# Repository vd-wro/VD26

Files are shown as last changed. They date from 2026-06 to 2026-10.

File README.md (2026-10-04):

# WRO VizDrive 2026


 

Welcome to the project repository for the **Panamanian 🔴⚪🔵 Team VizDrive** for the **World Robot Olympiad (WRO)** 2026!
Here you will find all the documentation, source code, images, and models related to our autonomous robot.

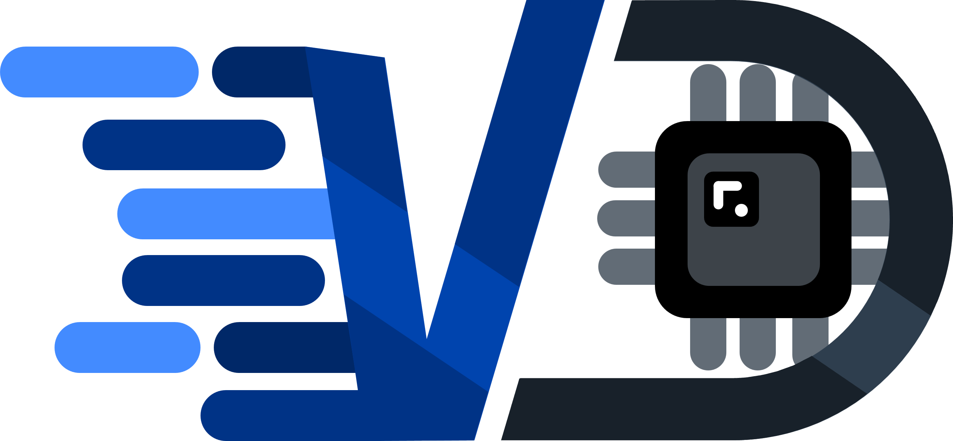
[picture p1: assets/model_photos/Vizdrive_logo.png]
Vizdrive Logo)


## About VizDrive's Legacy

VizDrive started in 2025, and now keeps thriving with the same young Panamanians that started the project. For this updated 2026 repository, we have kept ViZio's previous versions for better understanding and comparison from our engineering process.

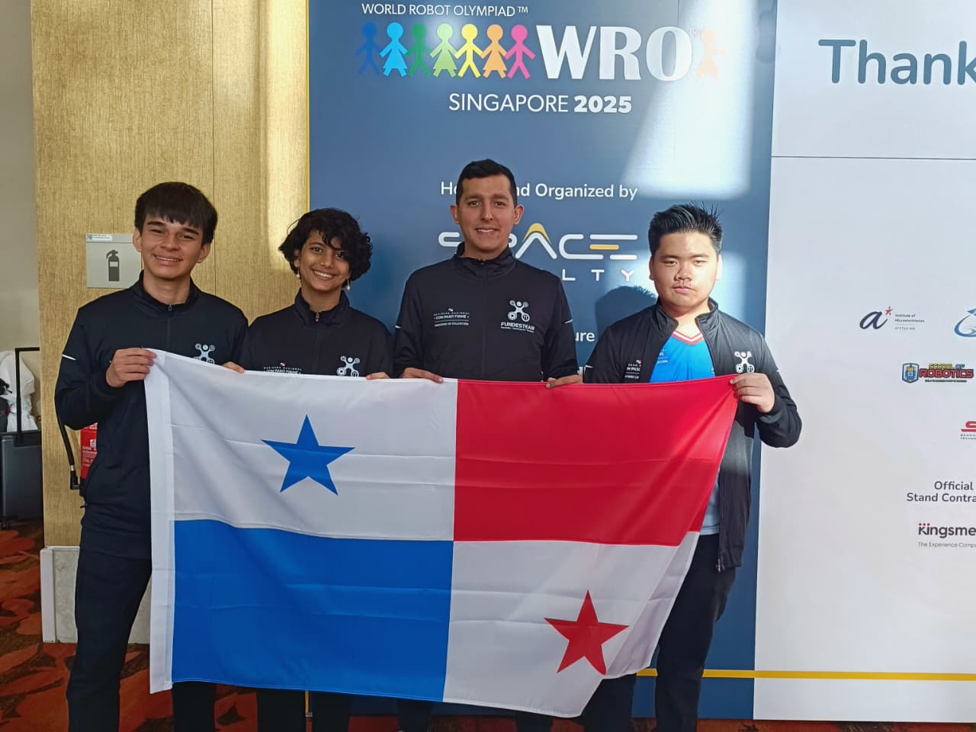
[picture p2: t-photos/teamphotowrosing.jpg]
Team


## Project Summary

VizDrive's core, ViZio, is an autonomous robot designed to navigate a closed-loop circuit, maintaining a stable trajectory with gyroscopic correction. It uses artificial vision, in conjunction with ultrasonic and color sensors, to detect walls and avoid obstacles.

Vizdrive Overview

We are participating in the **Future Engineers Category** to develop our skills and demonstrate the capabilities of young Panamanians in a competitive field like robotics.

During the creation of our robot, we tried to push the **fundamentals of robotics** to the highest we could. As you go through this GitHub repository, you may notice that we worked with very basic sensors (the kind typically found in standard Arduino kits), and that we strived to optimize them to the best of our capacities. This is because we aimed to make our build accessible for everyone, and show that even with the simplest components, it is possible to create truly functional robotic systems.

We would like to invite you into this short, 3 minute summary video to have a fresh start on our robot's construction, logic, and GitHub organization.

ViZio IV (https://www.youtube.com/watch?v=sTCSiO5S7kA)

> [!NOTE]
> Throughout the competition, we are constantly making modifications in the software and hardware of our robot. We try to update on all the changes we make, but if you notice any inconsistency between the pages of the documentation, please let us know!

---

## General Project Index

You can use this index to navigate through our robot's documentation. Each document provides detailed information on every aspect of its operation:

* [**1. General Project Overview**](./docs/01_project_overview.md)
  * General and concise introduction to the robot and its main components.
  * Describes the robot's operational phases and workflow diagram.
* [**2. Hardware and Components of the Robot**](./docs/02_hardware_components.md)
  * Detailed specifications of all integrated electronic and mechanical hardware.
  * [General Electromechanical Diagram](./schemes/electromechanical_diagram.png)
  * [Circuit Interactive Design (Cirkit)](https://vd-wro.github.io/VD26/embeds/interactive_circuit)
  * [KiCad Files](./src/kicad_pcb)
* [**3. Software Architecture**](./docs/03_software_architecture.md)
  * Overview of software libraries, core functionalities, and code structure.
  * [Autonomous Driving Code](./src/main_control/Vizdrive_WRO_code.ino)
* [**4. Sensor and Pin Configurations**](./docs/04_sensors_and_pin_configuration.md)
  * In-depth review of each sensor, its role in the functionality, and Arduino pin assignments.
  * [Sensors' Test Codes](./src/test_code/)
* [**5. Robot Mobility Functionality**](./docs/05_robot_mobility.md)
  * Focuses on the robot's motion system, motor configuration, and steering mechanisms.
* [**6. PID Control for the Gyroscope**](./docs/06_pid_gyroscope_control.md)
  * Explains the MPU gyroscope implementation and PID control for trajectory stability.
  * [MPU Calibration Code](./src/mpu_orientation_control/mpu_calibration/mpu_calibration.ino)
  * [MPU Calibration Data Graph](./assets/data_graphs/MPU%20Calibration%20Data%20Analysis.xlsx)
* [**7. Computer Vision Functions**](./docs/07_computer_vision.md)
  * Covers the PixyCam's vision-based obstacle evasion.
  * [Computer Vision Code](./src/computer_vision/computer_vision.ino)
* [**8. Ultrasonic Distance Sensing and PID**](./docs/08_ultrasonic_distance_sensing.md)
  * Covers the distance measurement and wall avoidance with ultrasonic sensors, and the filters implemented to adjust precision.
  * Introduces and explains the side PID system for straight-line driving.
  * [Ultrasonic Sensor Data Analysis](./assets/data_graphs/Ultrasonic%20Sensors%20Data%20Analysis.xlsx)
* [**9. Color Detection Functions**](./docs/09_color_detection.md)
  * Explains the color sensor's applications and calibration.
* [**10. 3D Modeling and Fabrication**](./docs/10_3d_modeling.md)
  * Details the 3D design process, mechanical characteristics, and fabrication parameters.
  * [3D Models STL](./models/)
* [**11. Other Resources and User Manual**](./docs/11_other_resources.md)
  * User manual for robot's construction and operation.
  * Summarized documentation and additional relevant resources and materials.
  * Evolution and improvements made within the versions of the robot.
  * Technical issues and applied fixes.

---

## ViZio Versions

| Versions | Problems | Improvements made | Used In | 
| :--- | :--- | :--- | :--- |
| Prototype | Often finding disconnected components. | N/a | First prototype made. |
| ViZio | Gyroscope calibration, partial parking, connection problems due to cable wear, complications with the dual ultrasonic sensor. radar. | Removed clutter with a hand-soldered PCB. | 🇵🇦 Regionals 2025 |
| ViZio 2.0 | Challenges with Pixy Parameters' calibration, incomplete parking maneuver, inverted SDA and SCL pins. | Improved PCB, kept one frontal ultrasonic, new logic for parallel parking. | 🇵🇦 National 2025 |
| ViZio V3 | Block color detection through Pixy, slower velocity. | Fixed PCB, adaption to camera bug, new parallel parking logic that includes last block evasion. | 🇸🇬 WRO 2025 |
| ViZio IV | Poor power distribution caused servo peaks to drain the battery | Changed camera, improved chassis, upgraded PCB, and added mechanical differential. | 🇵🇦 Regionals & National 2026 |
| ViZio Phase V |  N/a  | Coming soon... | 🇵🇷 WRO 2026 |

For better comprehension please visit [**Previous Versions of our Robot**](./docs/11_other_resources.md#119-version-history)

---

## Photos and Videos

* **Team Photos:** [View Photos](./t-photos/README.md)
* **Vehicle Photos:** [View Photos](./v-photos/README.md)
* **Demonstration Videos:** [View Videos](./video/README.md)

---

## Source Code

All control and test codes are located in the `src/` folder.

* [Autonomous Driving (Obstacle Avoidance)](./src/main_control/Vizdrive_WRO_code.ino)
* [Autonomous Driving (No Obstacle Avoidance)](./src/main_control/Open_Round.ino)
* [MPU Orientation Control (PID and Calibration)](./src/mpu_orientation_control/pid_gyroscope.ino)
* [Computer Vision (PixyCam 2.1)](./src/computer_vision/computer_vision.ino)
* [Sensors' Test Codes](./src/test_code/)

---

## 3D Models

Files for 3D printed components are located in the `models/` folder in `.stl` files.
To access interactive models of each component, hosted in GitHub pages, visit `embeds/`.

* [Robot 3D Models](./models/)
* [Interactive 3D Models](./embeds/)

A version of our Unity Simulator, used during the robot's construction and planification process, is available as an HTTP embed, hosted with GitHub pages.

* [Unity Simulator Information](./embeds/Unity_simulator)
* [Unity Web Player](https://vd-wro.github.io/VD26/embeds/Unity_simulator/)

---

## Diagrams and Graphs

Flowcharts, circuits, and relevant data graphs.

* [Operation Flowcharts](./assets/flowcharts)
* [Calibration Data Graphs](./assets/data_graphs/)
* [Additional Hardware Photos](./assets/hardware_photos/)

---

## Team Members 🙋‍♂️🙋‍♀️🙋

| | | |
|:---:|:---:|:---:|
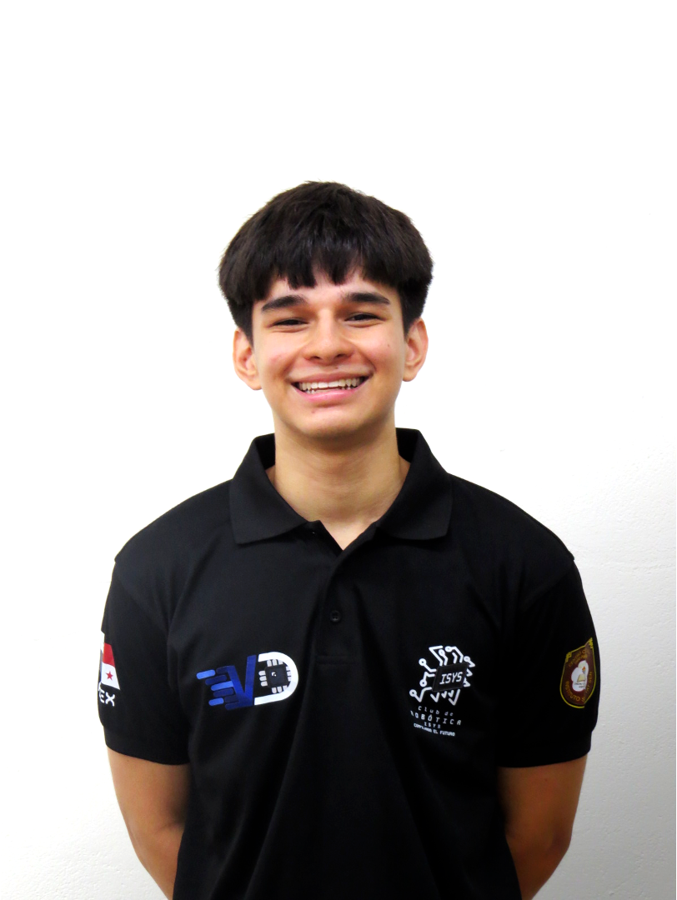
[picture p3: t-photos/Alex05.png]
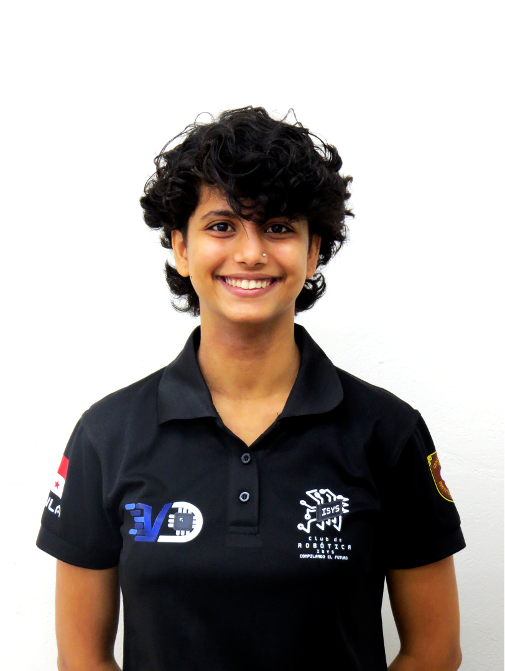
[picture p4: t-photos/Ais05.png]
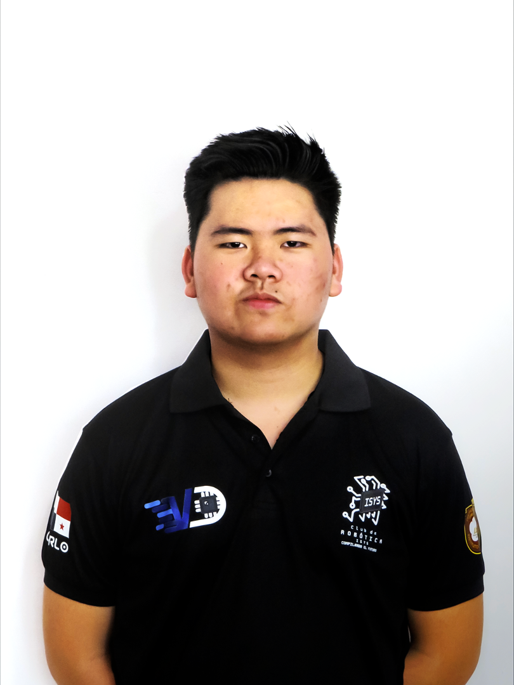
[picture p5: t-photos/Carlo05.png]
|  |  |  |
| [**ALEXIS PALACIOS NG**](./t-photos/meet_the_team/Alexis.md) <br> *Software Engineer* | [**AISLINN CHAWLA ARORA**](./t-photos/meet_the_team/Aislinn.md) <br> *Logistics and Creativity* |  [**CARLO HO NG**](./t-photos/meet_the_team/Carlo.md) <br> *Hardware Engineer* |
Sensor Integration, <br>Firmware Architecture, <br>Code Logic, <br>Error Management, <br>Data Analysis, <br>GitHub Repository | Engineering Journal, <br>Photography and Film, <br>Competition Planning, <br>Drafting, <br>Soldering, <br>GitHub Repository|  Construction, <br>Wiring, <br>Circuit and PCB Design, <br>Power Management, <br>3D Modeling and Planning, <br>Animation, Illustration, Editing  |

---

## Special Thanks

We are profoundly thankful to everyone who has supported us on our journey so far! We're incredibly grateful to our school administration for providing the resources and trust needed to pursue this challenge. To our teachers, thank you for your guidance and advice during our preparation; we especially appreciate your patience with our absences for robot practices (we promise to catch up on our assignments after the Olympiad 😅). A special shout-out to our friends who spent their free time supporting us, cheering us on, and helping us stay up to date. To our amazing parents, your assurance and belief in us have been the foundation of our efforts, allowing us to participate even though it meant missing many classes. And last but certainly not least, to our incredible coach, Professor Agustín Rogelio Orro Pérez. Even while mentoring five other teams, you still found time to guide us through it all. Your expertise, leadership, and dedication have been invaluable for us.

Thank you all!

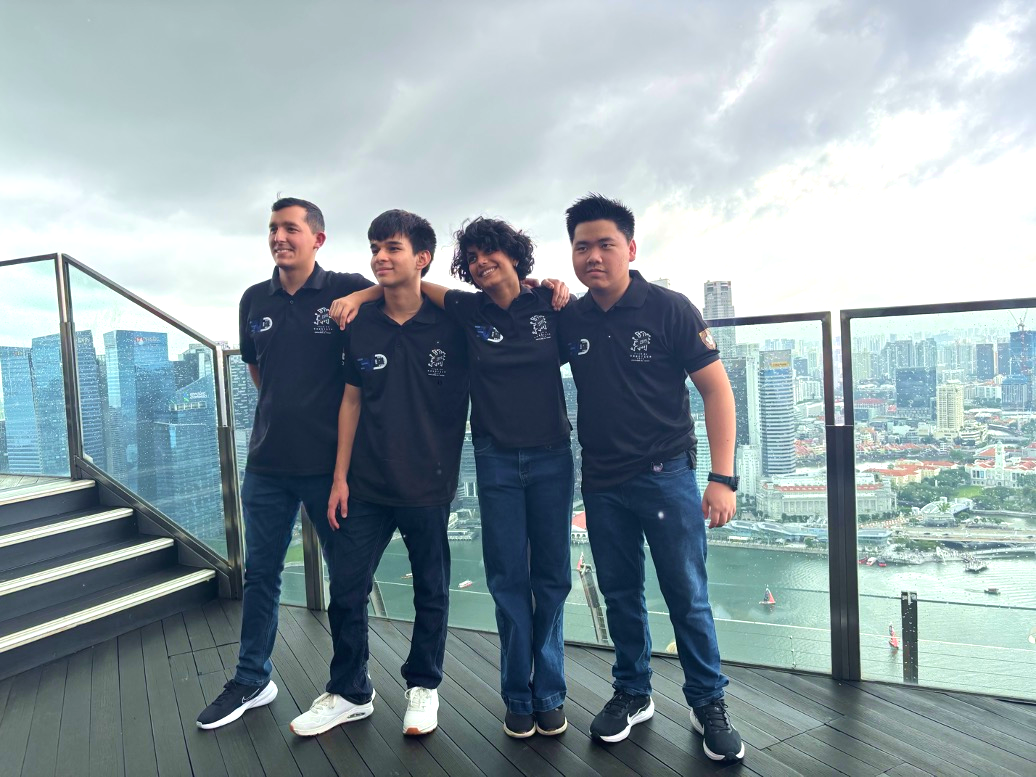
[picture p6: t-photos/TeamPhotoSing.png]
The Team


---

For any inquiry, question, or recommendation, feel free to contact us via email: **<vizdrive.wro@gmail.com>**

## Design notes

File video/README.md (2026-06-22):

# Robot Driving Demonstration Videos

Here are videos demonstrating our robot's autonomous driving capabilities for the WRO competition.

---

## Open Challenge Round Video

This video illustrates our robot's **MPU-6050 with PID orientation control**, coupled with **ultrasonic trajectory correction**.

For the Open Round, we adjusted our strategy because touching the outermost wall is prohibited. The robot's behavior in this video differs slightly from the complete code's. This adaptation is specifically for the Panamanian regional rounds, where the **center circuit configuration remains consistent**. In the full code, the robot prioritizes staying closer to the outermost wall to adapt to various environments.

Open Challenge Video (https://www.youtube.com/watch?v=nUoTaL3pmQw)

Previous versions of the robot share the same Open Round code and behavior; however, ViZio V3 now is able to navigate trough tighter spaces with the variable center.

Obstacle Challenge Video1 (https://www.youtube.com/watch?v=Y4y8UubQgvo)

---

## Obstacle Challenge Round Video

This video primarily showcases our robot's **artificial vision capabilities** using the **PixyCam 2.1**. It also features trajectory correction based on the MPU and PID control, supplemented by intentionally colliding with the outermost wall for a hard correction. If you observe closely, you'll also notice the subtle ultrasonic correction, which ensures the PixyCam consistently detects obstacles and reacts appropriately.

Updated regional practice video:

Obstacle Challenge Video1 (https://www.youtube.com/watch?v=GUYxAUy47Ms)

National close-up practice video:

Obstacle Challenge Video2 (https://www.youtube.com/watch?v=BSdScv6dc1I)

International event practice video:

Obstacle Challenge Video3 (https://www.youtube.com/watch?v=nUtFuM8RD_c)

You can also check our YouTube channel for more Obstacle Challenge videos.

# Robot Animation Video

These videos serve as supplementary material and explanations of the robot's assembly.

This video shows how to assemble all ViZio's parts and components into the chassis 3D Model.

Robot Animation Video1 (https://www.youtube.com/watch?v=Cte4G7Wkx94)

The second video explains all the changes made to our robot's updated version.

Robot Animation Video2 (https://www.youtube.com/watch?v=JOWvUNmzN1w) 

This is the third video, explaining the building process of ViZio's 3rd version.

Robot Animation Video3 (https://www.youtube.com/watch?v=J1BOTFqHlQ4) 

Fourth video, an introduction of what our latest model's improvements

ViZio IV (https://www.youtube.com/watch?v=X2UGbEu-D34)

Differential assembly video, an animation of the building process of ViZio's new mechanical differential system.

ViZio IV (https://www.youtube.com/watch?v=UHFCzMF-fk8)

# Music Creation Video (Easter egg!)

Not only the 3D models are created by us, the music as well is a personal composition for each video!
Soon the video explaining the music creation process will be uploaded to our Instagram Profile. 



---

[Back to Main README.md Index](../README.md)

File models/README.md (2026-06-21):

# Models Folder

Here you can find all the .stl and .glb models of every 3D modeled part of our robot.

The .glb models are used for the HTML embeds hosted in GitHub pages. 
We designed these embeds for a more interactive visualization of the models and their colors in the real-life robot. However, the .stl files can also be visualized directly in GitHub.

The designs included in this file directory are:

## 1. Chassis Model

| Old Model | New Robot | International Robot | 2026 Robot |
| :---: |  :---: |  :---: |  :---: |
| [Chassis](./chassis/chassis.stl) | [New Chassis](./chassis/chassis2.0.stl) | [International Chassis](./chassis/ViZioInternationalMotorFix.stl) | [2026 Chassis Moddels](./../docs/10_3d_modeling.md#chassis) |
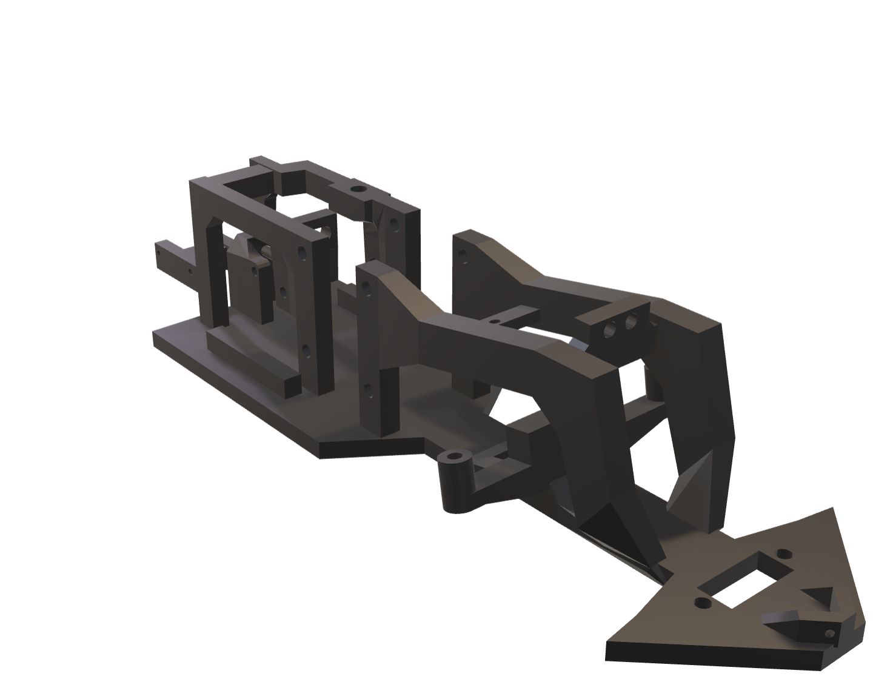
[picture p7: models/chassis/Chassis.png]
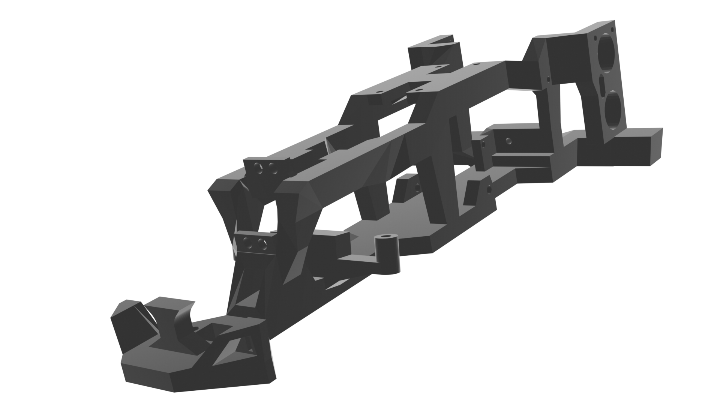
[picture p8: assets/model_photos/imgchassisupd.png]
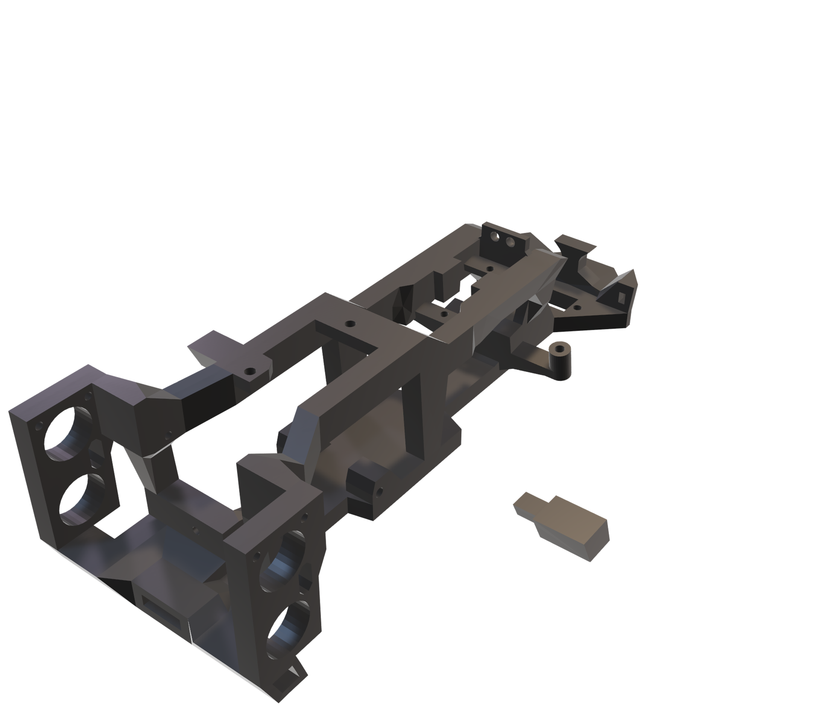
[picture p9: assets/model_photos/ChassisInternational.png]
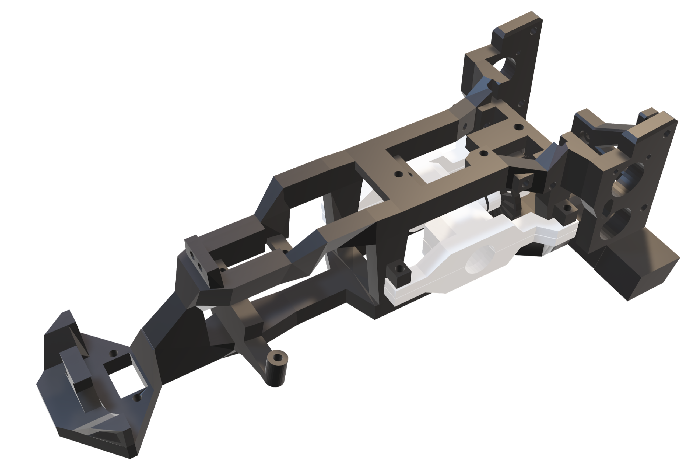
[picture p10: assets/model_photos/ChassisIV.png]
|  |  |  ||
| Visit the embed: [Chassis Embed](https://vd-wro.github.io/VD26/embeds/interactive_chassis)| Visit the updated embed: [Updated Chassis Embed](https://vd-wro.github.io/VD26/embeds/interactive_chassis2) | Visit the latest version: [International Chassis Embed](https://vd-wro.github.io/VD26/embeds/chassis_final) | [2026 Chassis Embed](https://vd-wro.github.io/VD26/embeds/chassis_26) |

## 2. Steering

### 1. [Steering Rod and Camera Support](./steering/steering_rods.stl)
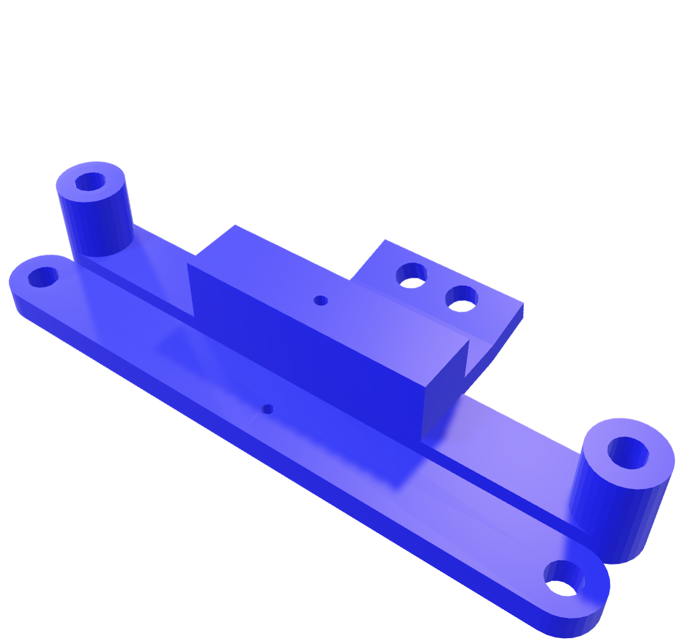
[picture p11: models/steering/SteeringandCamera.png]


Visit the embed: [Steering Rod and Camera Support Embed](https://vd-wro.github.io/VD26/embeds/interactive_steering_rods)

## 3. Wheels Models

### 1. [Wheel Hubs](./wheels/wheel_hub.stl)
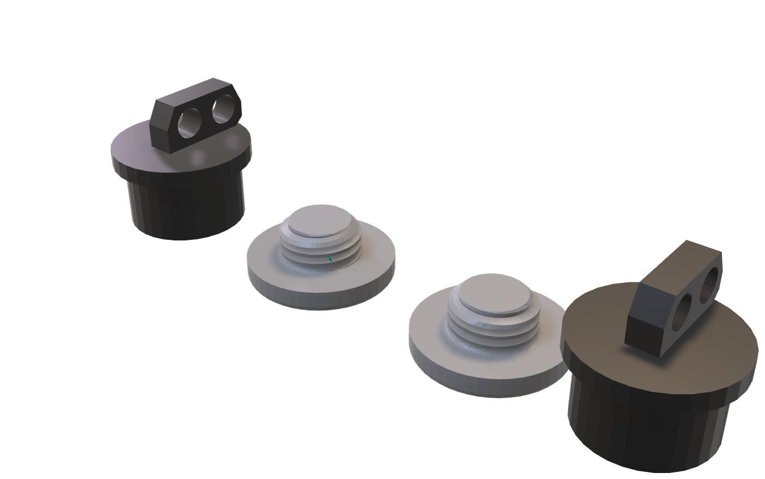
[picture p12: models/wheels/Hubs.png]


Visit the embed: [Wheels Hub Embed](https://vd-wro.github.io/VD26/embeds/interactive_hub)

### 2. [Rear Wheels](./wheels/encoder_wheel.stl) - [Rear Wheels IV](./wheels/ViZio26CalcModel_WheeL.stl)
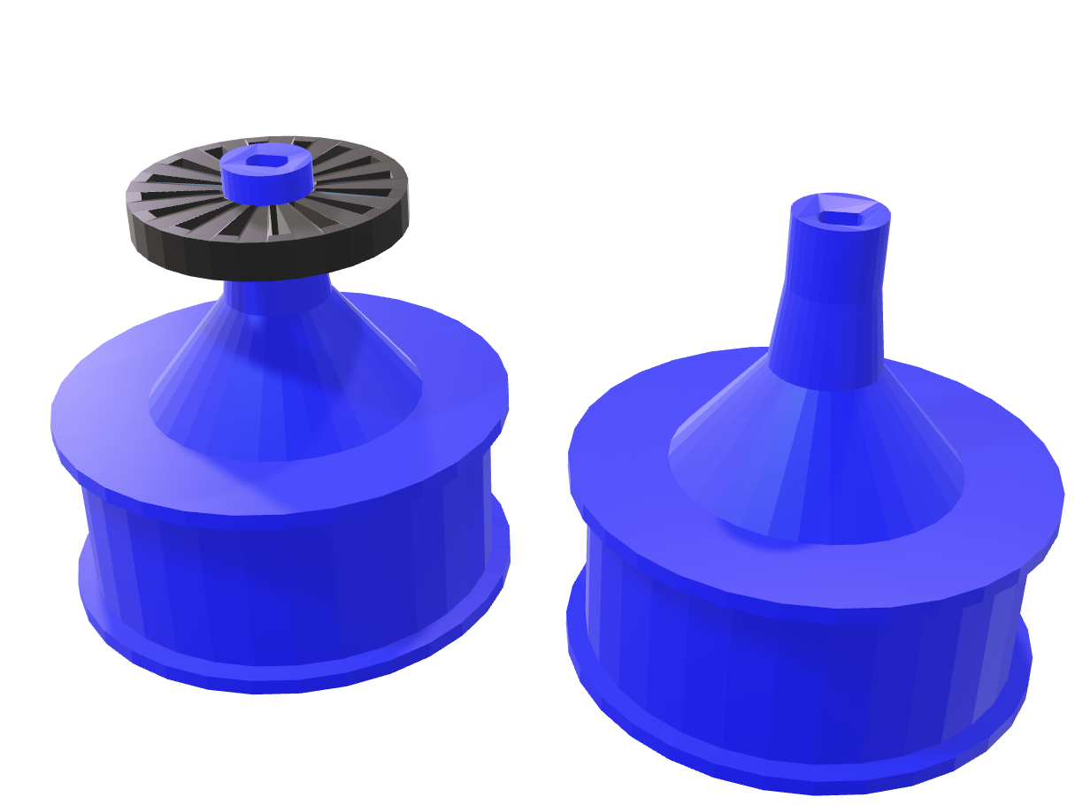
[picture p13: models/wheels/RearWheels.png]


Visit the embed: [Rear Wheels Embed](https://vd-wro.github.io/VD26/embeds/interactive_rear_wheels)

### 3. [Wheel Rims](./wheels/wheel_rims.stl)
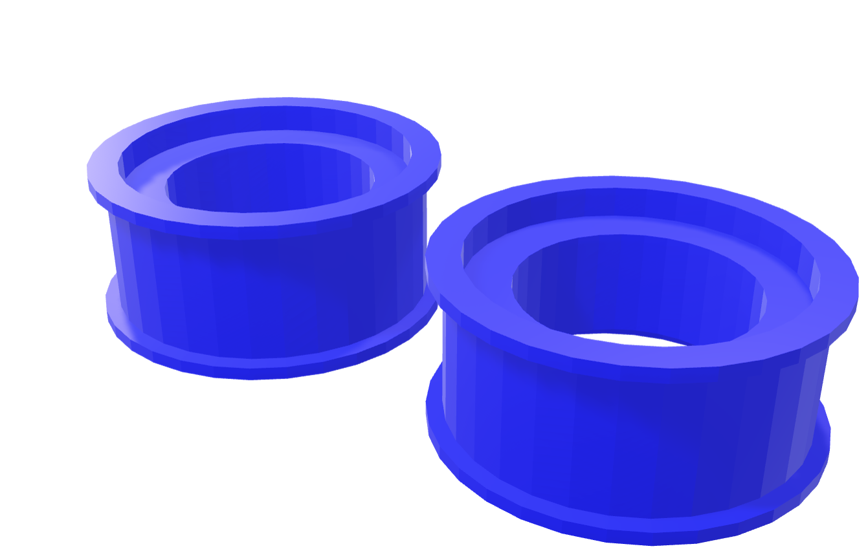
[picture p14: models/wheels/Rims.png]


Visit the embed: [Wheel Rims Embed](https://vd-wro.github.io/VD26/embeds/interactive_rims)

---

For an explanation on the design and 3D printing of these models, refer to the document: [**10. 3D Modeling**](../docs/10_3d_modeling.md)

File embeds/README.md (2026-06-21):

# Embeds

This folder contains the HTML JavaScript embeds for the **Unity Simulator**, **interactive 3D models** and **circuit design**.

The Unity Simulator was created during the robot's designing process. It is made with Unity, for sensors and physics simulation. For more information, visit its separated folder [Unity Simulator](./Unity_simulator).

The interactive models are presented in web pages and allow users to view and manipulate 3D objects directly in their browser.
We opted to include this feature primarily to address the limitations of GitHub's .stl file visualization, which lacks color support and offers restricted viewing capabilities.

On the other hand, the interactive circuit was designed using the **Cirkit Designer App**. This platform is ideal for understanding the component connections to the Arduino MEGA 2560 Embed, especially with its built-in chatbot and pin visualization features.

---

## Visualize the different interactive components

### [Robot Simulator with Unity](https://vd-wro.github.io/VD26/embeds/Unity_simulator/)

### [Interactive Circuit Diagram](https://vd-wro.github.io/VD26/embeds/interactive_circuit)

### [Interactive Chassis](https://vd-wro.github.io/VD26/embeds/interactive_chassis)

### [Updated Interactive Chassis](https://vd-wro.github.io/VD26/embeds/interactive_chassis2)

### [International Interactive Chassis](https://vd-wro.github.io/VD26/embeds/chassis_final)

### [2026 Interactive Chassis](https://vd-wro.github.io/VD26/embeds/chassis_26)

### [Interactive Hub](https://vd-wro.github.io/VD26/embeds/interactive_hub)

### [Interactive Rear Wheels](https://vd-wro.github.io/VD26/embeds/interactive_rear_wheels)

### [Interactive Rims](https://vd-wro.github.io/VD26/embeds/interactive_rims)

### [Interactive Steering Rod](https://vd-wro.github.io/VD26/embeds/interactive_steering_rods)

### [Interactive KiCad PCB](https://vd-wro.github.io/VD26/embeds/Interactive_KiCad_PCB)

### [Interactive Robot Viewer](https://vd-wro.github.io/VD26/embeds/Robot)

## How These Embeds Work

## Interactive 3D Models

The HTML codes creates a simple web page that displays an **interactive 3D model**. It uses the `<model-viewer>` web component, the tool that makes it easy to embed 3D models on the web with capabilities like augmented reality (AR) and user controls.

**Example:** interactive_chassis.html

### HTML Structure (`<!DOCTYPE html>`, `<html>`, `<head>`, `<body>`)

* **`<!DOCTYPE html>` and `<html lang="es">`**: Standard declarations defining the document type as HTML5 and setting the language to Spanish.
* **`<head>`**: Contains metadata about the page:
    * **`<meta charset="UTF-8">`**: Specifies the character encoding, ensuring text displays correctly.
    * **`<meta name="viewport" content="width=device-width, initial-scale=1.0">`**: Configures the viewport for responsive design, making the page look good on various devices.
    * **`<title>Car Chassis Interactive 3D Model</title>`**: Sets the title that appears in the browser tab.
    * **`<script type="module" src="https://ajax.googleapis.com/ajax/libs/model-viewer/3.4.0/model-viewer.min.js"></script>`**: This is the most crucial line for the 3D model. It imports the **`model-viewer`** library, a web component developed by Google. This script enables the custom `<model-viewer>` HTML tag to display 3D models. The `type="module"` ensures it's loaded as an ES module.
    * **`<style>`**: Contains **CSS (Cascading Style Sheets)** rules that define the visual appearance of the web page. This includes:
        * Centering content on the page (`body`).
        * Styling the headings (`h1`).
        * Defining the size, background, border, and shadow for the `<model-viewer>` element itself.
        * Styling for the `controls` section and links (`a`).

### Body Content (`<body>`)

* **`<h1>Interactive 3D Model</h1>` and `<h1>Car Chassis</h1>`**: These are headings that display the title of the interactive model on the web page.
* **`<model-viewer>` Tag**: It's a custom HTML element provided by the `model-viewer` library.
    * **`src="./models_glb/chassis.glb"`**: This attribute points to the 3D model file itself. The `.glb` format is a binary version of glTF, optimized for efficient loading and transmission.
    * **`alt="Chassis 3D Model"`**: Provides alternative text for accessibility, describing the content for screen readers.
    * **`ar`**: Enables **Augmented Reality (AR)** functionality. If the user's device supports it, they can view the 3D model placed in their real-world environment using their camera.
    * **`shadow-intensity="1"`**: Controls the strength of the shadow cast by the 3D model.
    * **`camera-controls`**: This is essential for user interaction. It allows users to **rotate, pan, and zoom** the 3D model using their mouse or touch gestures.
    * **`touch-action="pan-y"`**: Specifies how touch gestures are handled. `pan-y` allows vertical panning while reserving horizontal movement for model rotation, which can improve user experience on touch devices.
    * **`autoplay`**: Makes the model automatically animate or rotate when it loads.
    * **`exposure="1.2"`**: Adjusts the brightness of the model's lighting.
    * **`environment-image="neutral"`**: Sets the ambient lighting environment for the model. "neutral" provides a balanced lighting setup.
    * **`bounds="tight"`**: Causes the camera to tightly frame the model.
    * **`tone-mapping="neutral"`**: Controls how colors are rendered, aiming for a natural look.
    * **`loading="eager"`**: Instructs the browser to load the model as soon as possible.
    * **`` and ``**: These are optional slots for custom elements that `model-viewer` can display. The `poster` slot is typically used for an image shown before the model loads, and the `progress-bar` slot is for a loading indicator. They are empty, so they won't visibly do anything unless styled with CSS or filled with content.

* **`<div class="controls">`**: This section provides **user instructions** for interacting with the 3D model.
    * It explains how to rotate (drag with mouse/finger) and how to zoom (mouse wheel/pinch).
  
* **`<p><a href="javascript:history.back()">Go back to main page</a></p>`**: A simple paragraph with a link that, when clicked, uses JavaScript (`history.back()`) to navigate the user to the previous page in their browser history.

## Interactive Circuit Diagram

This HTML code creates a simple web page designed to **embed an interactive circuit diagram** hosted on the Cirkit Designer platform.

### HTML Structure 

It's a standard HTML5 page with a basic `head` (containing metadata and styling) and a `body` (with the visible content).

* **Styling (`<style>` tag)**: The CSS here primarily focuses on making the embedded content **responsive**.
    * `embed-container`: This class uses a common trick for responsive embeds. By setting `position: relative` and using `padding-top` based on `width`, it creates an aspect ratio that ensures the `iframe` (which is `position: absolute` inside it) scales correctly while maintaining its proportions. The `calc(max(56.25%, 400px))` ensures the height is at least 400px or scales with a 16:9 aspect ratio, whichever is larger.
    * `iframe`: Styles the `iframe` to fill its container and removes the default border.
* **Content**:
    * **Headings and Paragraphs**: Provide a title for the page and instructions for the user (e.g., "Click on 'Explore this Circuit' to interact with the model and access the Cirkit chatbot.").
    * **The `<iframe>`**: This is the core of the embed.
        * `src="https://app.cirkitdesigner.com/project/c9dde92c-847c-48cf-9794-15c1a4459869?view=interactive_preview"`: This attribute points to our specific project on the Cirkit Designer platform. The `?view=interactive_preview` parameter tells Cirkit to display the project in an interactive, embeddable preview mode.
    * **Links**:
        * One link allows users to directly **edit the project** in Cirkit Designer (opening in a new tab due to `target="_blank"`).
        * The link, `javascript:history.back()`, allows users to **navigate back** to the previous page in their browser history.

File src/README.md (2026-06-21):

# Souce Code Directory

Here you can find all the .ino files for the operation of our robot in the Open and Obstacle Challenges.
As well, you can find the test codes we used throughout the process of construction and debugging, besides the codes for data recolection and analysis for the ultrasonic sensors and the MPU6050.

The directory is organized in the following way:

## `src/07_computer_vision`

You will find the test code for the Pixycam 2.1 artificial vision and color signature detection. 

## `src/main_control`

You'll find the updated main code for the WRO competition challenges.

When you refer to the main source code, please consider that it is updated throughout the competition to improve or add different features, so it may vary between rounds.
In particular, the PID control constants, the amount of correction, and the different thresholds are modified depending on the performance.
You can see progress and changes over time by viewing previous versions in GitHub commits.

## `src/mpu_orientation_control`

You will find the test code and data recolection code for the MPU6050 gyroscope + accelerometer.

## `src/ultrasonic_sensors`

You will find the test code for raw measurements, the test code for filtered measurements, and the code for data recolection to compare how the error dispersion varies between raw and filtered measurements.

## `src/test_code`

You will find the general test codes for other functionalities as the color sensors suite, mainly to adjust the thresholds, or a code to test the motor and IR encoder.

## `src/kicad_pcb`

You will find the circuit files for our custom PCB.

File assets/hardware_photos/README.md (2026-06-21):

# Hardware Photos

This folder contains additional photos of our robot's hardware, components, and circuitry.
Especially older versions of our robot.

For the more updated pictures of the vehicle from all angles, refer to the [**`/v-photos`**](../../v-photos) folder.

## Preview

### Previous version of our robot.

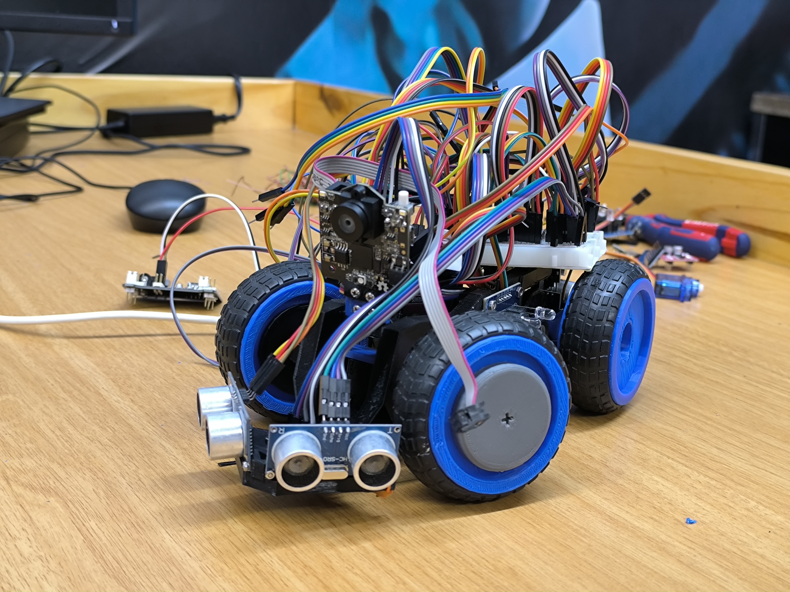
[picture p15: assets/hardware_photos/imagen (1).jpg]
imagen 1

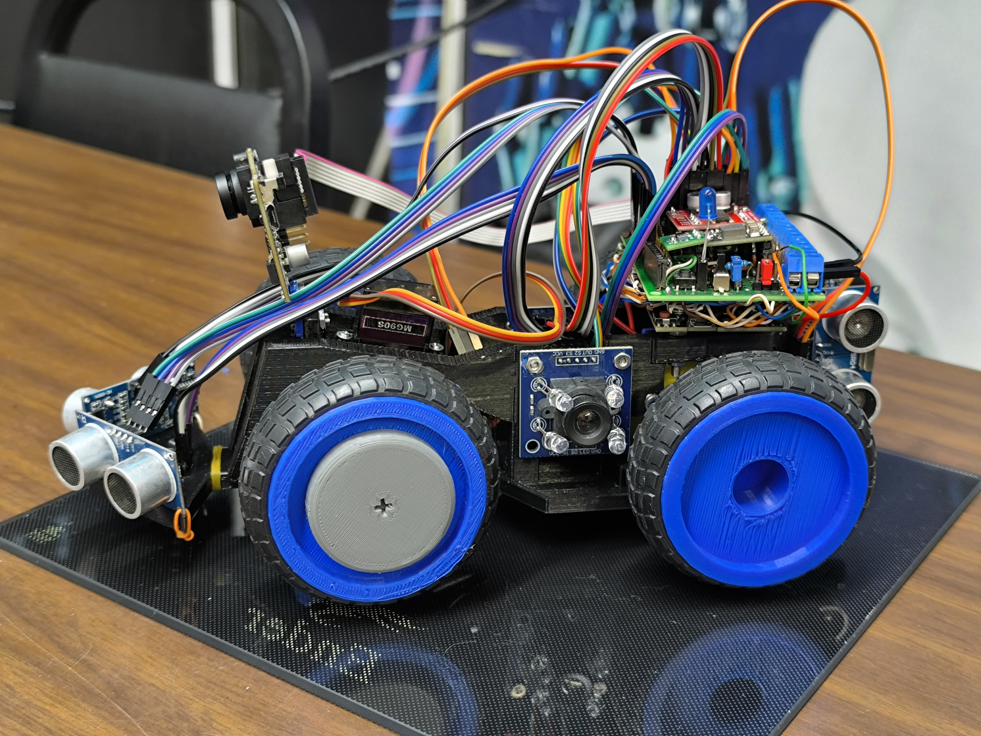
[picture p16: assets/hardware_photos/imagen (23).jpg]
imagen 2

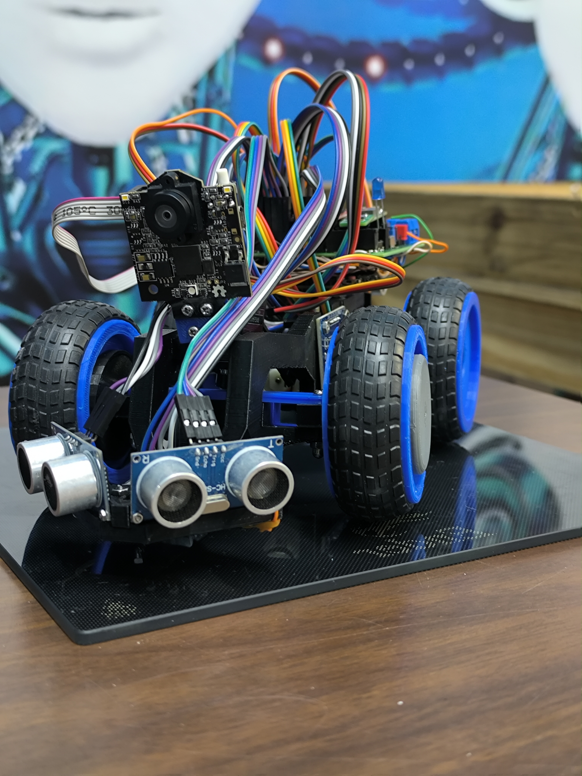
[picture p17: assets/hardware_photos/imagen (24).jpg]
imagen 3

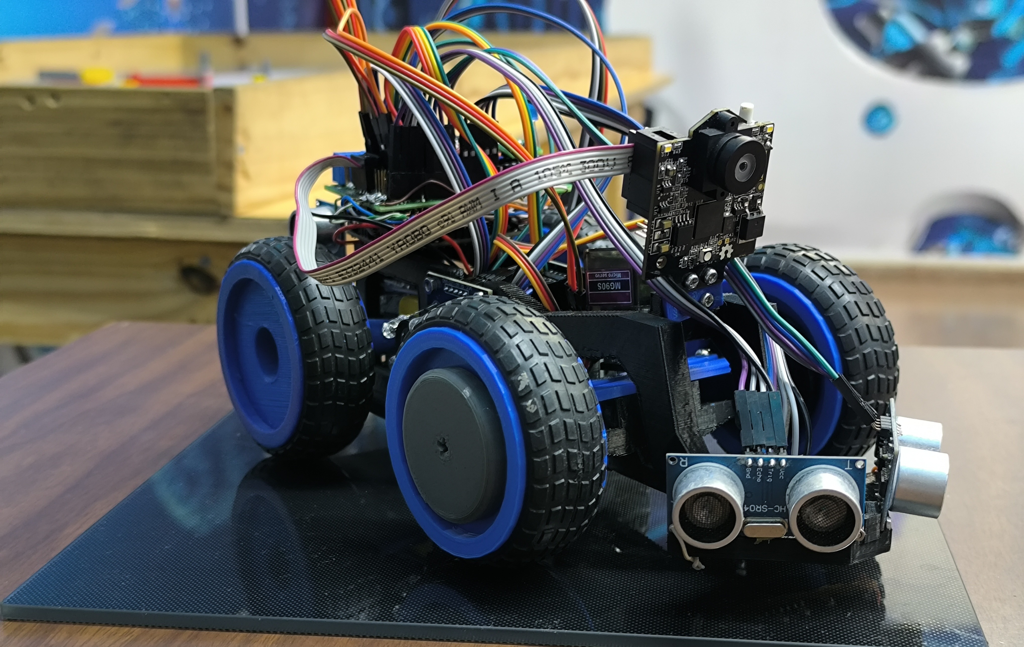
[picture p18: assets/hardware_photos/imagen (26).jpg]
imagen 4

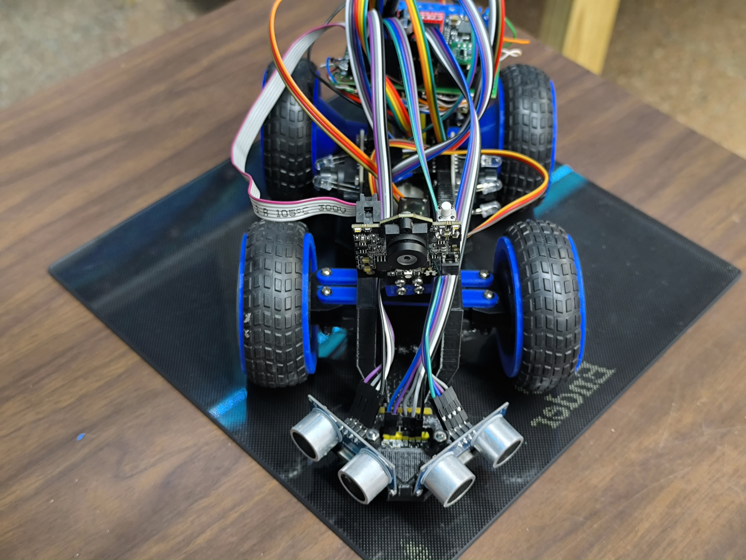
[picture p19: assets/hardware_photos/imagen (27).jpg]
imagen 5

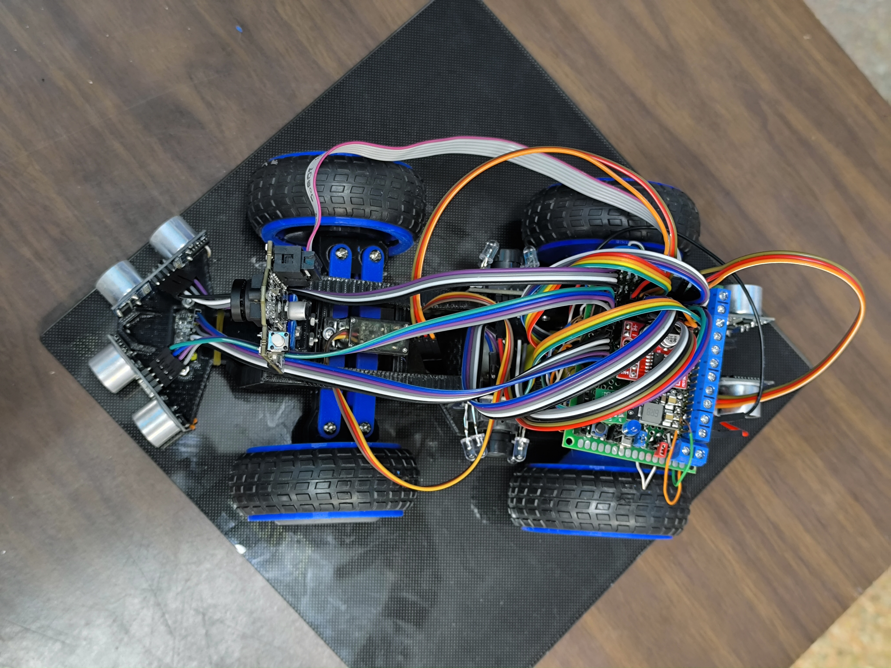
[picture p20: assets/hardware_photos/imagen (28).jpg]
imagen 6

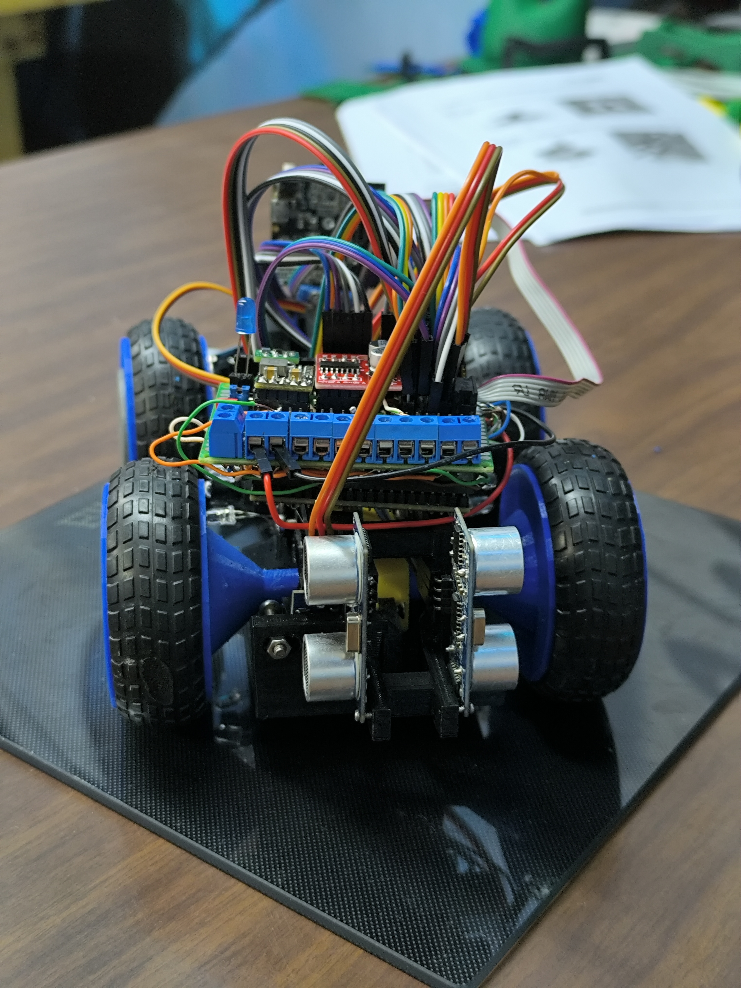
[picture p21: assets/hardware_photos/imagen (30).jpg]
imagen 7


### PCB Design and Arduino Mega Chip

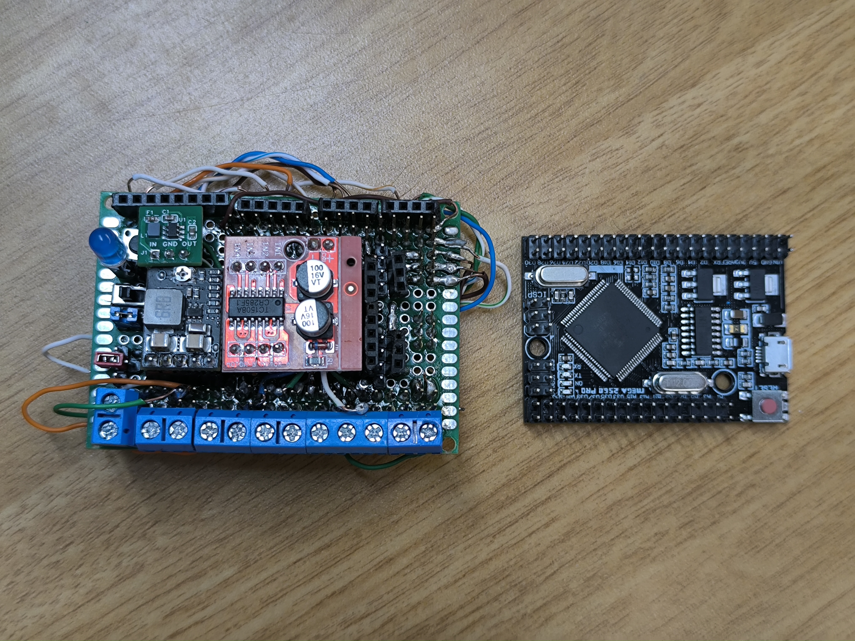
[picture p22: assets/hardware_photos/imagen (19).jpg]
imagen 8


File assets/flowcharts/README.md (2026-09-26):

# Workflow Diagram

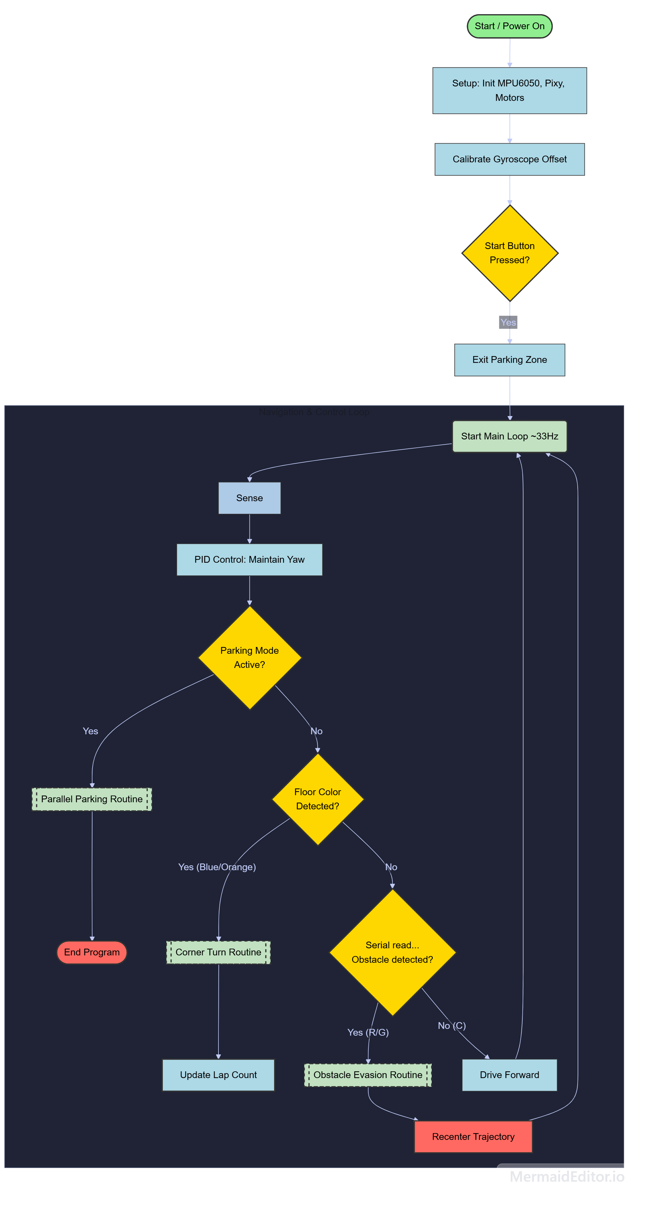
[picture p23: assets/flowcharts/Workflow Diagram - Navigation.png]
Main Workflow Diagram


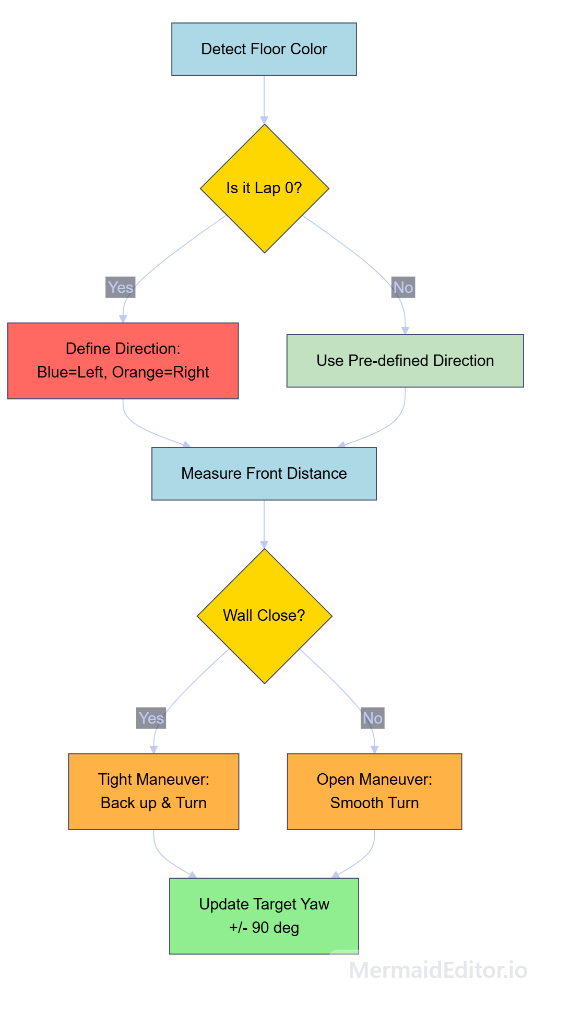
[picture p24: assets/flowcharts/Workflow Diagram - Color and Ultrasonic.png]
Color and Ultrasonic Workflow Diagram


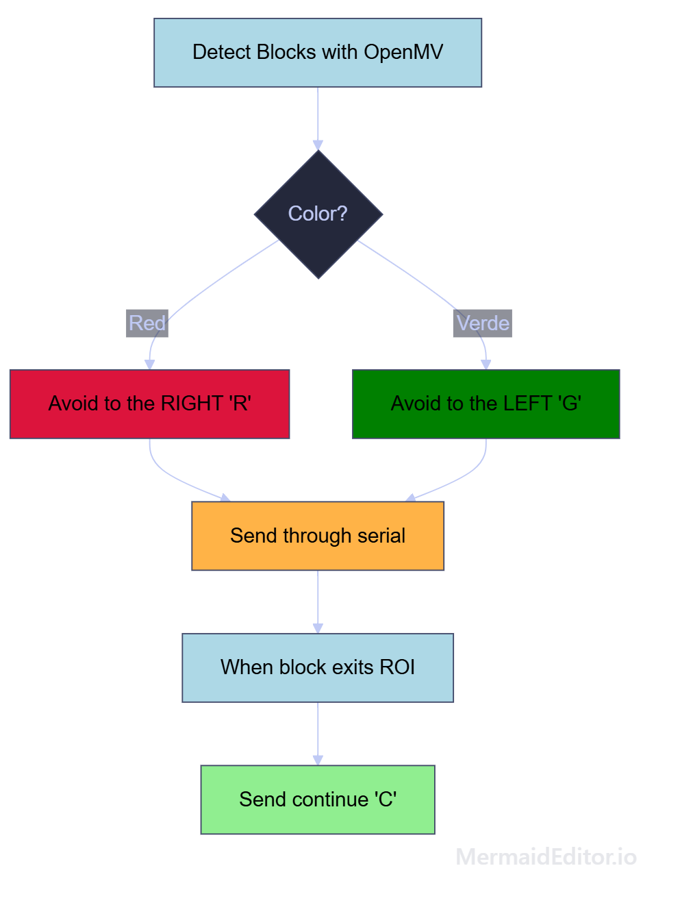
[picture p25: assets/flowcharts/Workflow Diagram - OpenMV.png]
OpenMV Workflow Diagram


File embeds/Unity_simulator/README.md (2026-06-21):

# Unity Simulator

During the robot's design and build phase, we developed a Unity simulator.
This simulator was utilized to define the robot's core logic, optimize sensor and actuator placement, and refine its overall functionality.

Unity was an ideal choice due to its robust PhysX physics engine (simulating collisions, gravity, and friction), accurate sensor and camera emulation (providing the robot's perspective and sensory input), and C# scripting capabilities, which allowed us to prototype code similar to the real robot.

Testing before physical prototyping is essential for any robot build, and [simulation with Unity](https://unity.com/es/blog/engine-platform/robotics-simulation-is-easy-as-1-2-3) is becoming more and more common for modern robot engineering.

Visit the [**Unity Web Player**](https://vizdrive.github.io/VizDrive_WRO2025/embeds/Unity_simulator/) preview hosted on GitHub pages. Please note that this is an optimized and simplified version, necessary due to the the maximum file size in GitHub.

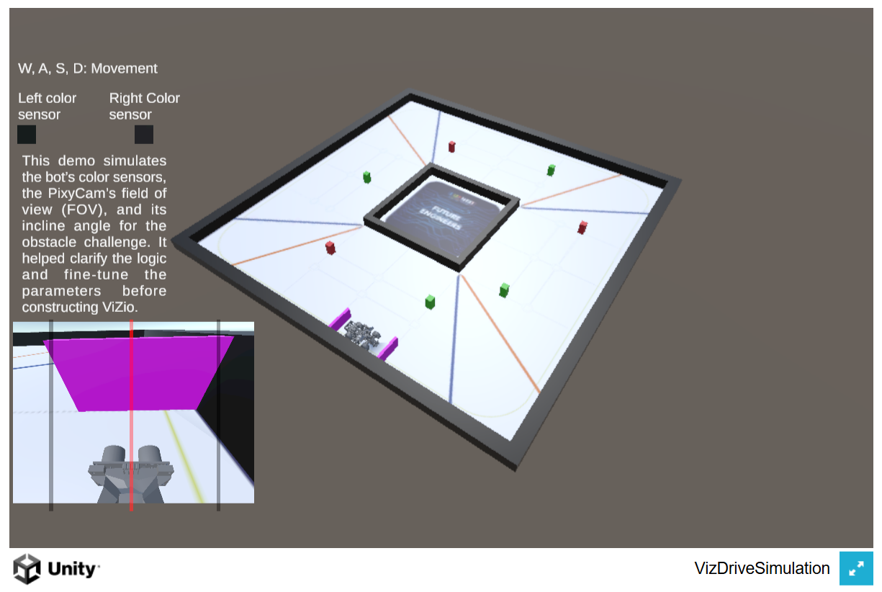
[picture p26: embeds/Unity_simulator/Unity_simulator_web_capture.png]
Unity Simulator Web Capture


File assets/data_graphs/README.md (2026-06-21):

# Data Graphs

This folder refers to the data graphs of our sensor suite calibration.

## MPU6050 Calibration and Data Analysis

The MPU6050 gyroscope + accelerometer is calibrated with live sample readings, to being able to adapt to any environment.
It calculates the average of 250 samples measured when the robot is static, averaging out the bias. This offset is subtracted from all subsequent raw readings for accuracy.
The data recolection, shows that **250** samples is enough to achieve a precision of ±0.01, which is enough for the robot's functionality.

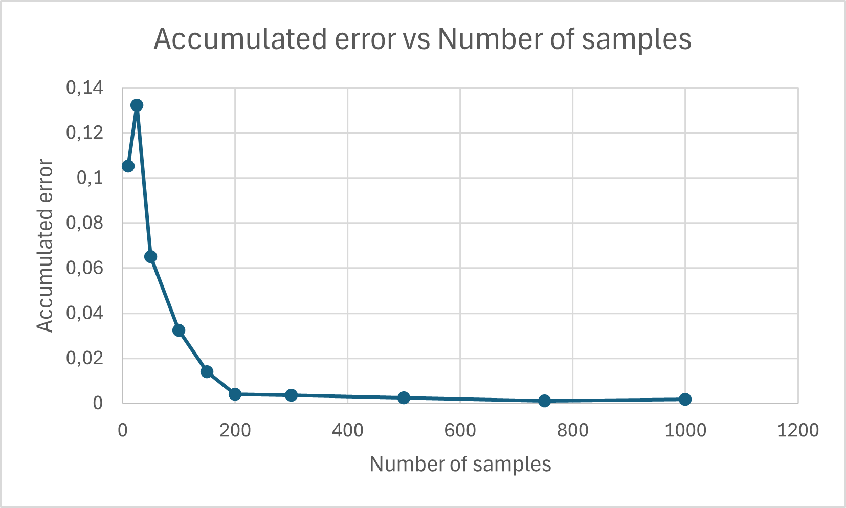
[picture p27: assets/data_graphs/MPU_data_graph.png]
MPU Data Graph


For more information on the MPU6050 control logic and calibration, refer to: [6. PID and Gyroscope Control for Orientation](./../../docs/06_pid_gyroscope_control.md)

## Ultrasonic Sensors Filter Control and Data Analysis

HC-SR04 ultrasonic sensors always present a certain level of noise when collecting many measurements consecutively.
Our robot needs to avoid outliers to maintain a consistent performance. Even one measurement that deviates from what is expected could cause the robot to stop operating properly.

To prevent this malfunction, two filters are implemented for ultrasonic sensors: an outlier filter (similar to a median filter) and a filter to ignore very distant or very close values.
The graph shows how the error dispersion changes when applying our filter to an ultrasonic sensor, measuring the same length.

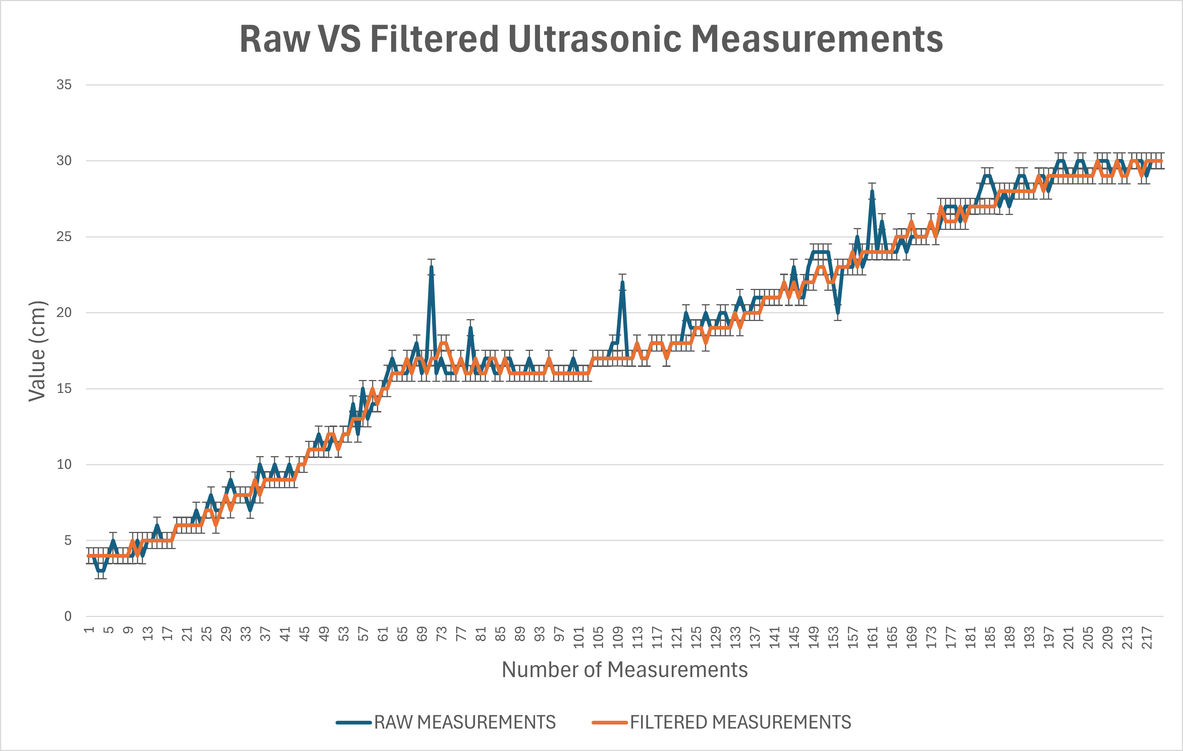
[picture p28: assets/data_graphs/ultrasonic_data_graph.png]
Ultrasonic Sensors Data Graph


For more information on the Ultrasonic Sensor suite, refer to: [8. Ultrasonic Distance Sensing](./../../docs/08_ultrasonic_distance_sensing.md)

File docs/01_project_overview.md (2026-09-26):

# 1. Project Overview

## 1.1 Introduction to VizDrive 2026

ViZio is an autonomous robot developed by a Panamanian 🔴⚪🔵 Team VizDrive for the **2025 and 2026 World Robot Olympiad (WRO)**.
Our project participates in the **Future Engineers** category. Our goal is to apply advanced robotics, data analysis, error management, and optimization principles to represent Panama again in the international field of robotics.

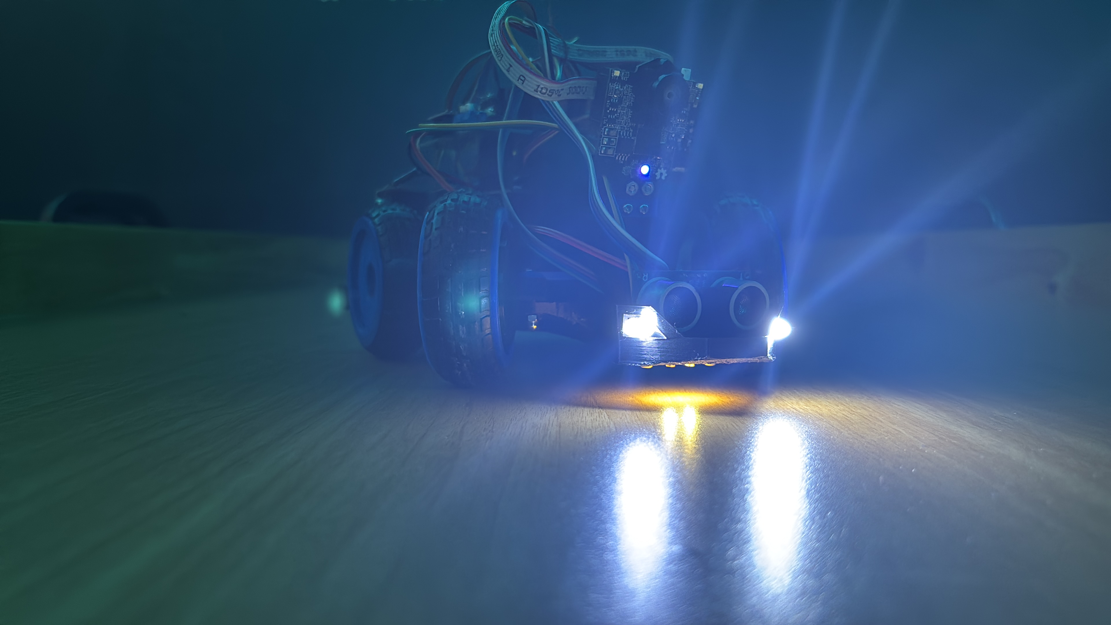
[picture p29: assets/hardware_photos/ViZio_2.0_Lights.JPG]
Vizdrive Overview


The primary objective of ViZio is to autonomously navigate a predefined closed-loop circuit, and to detect and evade obstacles. This is achieved using a combination of artificial vision for obstacle detection, and an array of sensors for decision-making. Every single part of the robot is designed, optimized, and constructed by the VizDrive Team.

In the Future Engineers category, we compete in two distinct challenge rounds: the **Open Challenge** and the **Obstacle Challenge**. While the robot shares most of its core functionalities across both rounds, there are key adjustments between the two. For clarity, we present the robot as a unified system in this documentation, and highlight the specific differences as they arise.

## 1.2 Main Components

| Component | Function |
| --- | --- |
| **DC Motor** | Employed for rear-wheel drive (RWD) propulsion. |
| **Wheel Encoder** | Measures the rotational pulses per revolution (PPR) of the wheels, used for odometry and precise maneuvers. |
| **Servo Motor** | Utilized for steering control of the front wheels. |
| **OpenMV H7 Plus** | Responsible for obstacle recognition and color-based detection. |
| **Ultrasonic Sensors** | Measures real-time distance to walls, used for turns and collision avoidance. |
| **MPU Gyroscope with PID Control** | Provides continuous orientation data, which is processed by a Proportional-Integral-Derivative (PID) controller, to ensure stable and straight trajectory. |
| **Color Sensor** | Employed for detecting specific colored lines marked on the circuit, signaling turns. |

Each of these parts have their own separated document, delving into their calibration, common errors, logic and function in the robot.

## 1.3 Dimensions

| Specification | Information |
| --- | --- |
| Height | 15 cm |
| Width | 14 cm |
| Length | 26 cm |
| Weight | 841 g |

---

## 1.4 Main Operational WorkFlow

The robot's operation can be divided into three phases:

### 1. **Initialization Phase (Setup):**

* **Power-Up**, **Self-Checks** and **Calibration:** upon power-up, the robot ensures all sensors and actuators are operational, and calibrates the MPU gyroscope yaw angle for orientation. If a sensor is not initialized correctly, the program will not start.
* **Waiting for Start:** when the robot is ready for operation an LED indicator illuminates to signal readiness, and the program starts upon a button press.

### 2. **Autonomous Navigation Phase:**

This is the primary operational phase, a loop where the robot continuously checks and adapts to its environment:

* **Orientation Correction (Continuous):**
  * The **MPU-6050** provides real-time orientation data.
  * This data is fed into a dedicated PID (Proportional-Integral-Derivative) controller, which compensates for any rotational drift, ensuring the robot maintains a stable and straight heading throughout its trajectory.
  * To correct the **MPU-6050's accumulated offset**, in the **Obstacle Challenge**, the robot uses the rear wall to **reset its yaw angle**. On the other hand, in the **Open Challenge**, it uses the robot's **parallel distance to the wall**.
* **Obstacle Detection and Evasion (Conditional):**
  * While maintaining trajectory, the **OpenMV H7** constantly scans the path ahead for obstacles.
  * If an obstacle is detected within the predefined **Region of Interest (ROI)** of the camera's field of view:
    * **Evasion Maneuver:** the robot turns until the obstacle is no longer detected within the OpenMV's ROI. The objects enter a "safe area" depending on the color, which indicates s obstacles are already evaded.
    * **Re-acquisition of Trajectory:** following an evasion maneuver, the robot re-establishes its MPU-based trajectory correction. Concurrently, side ultrasonic sensors are utilized to assist in re-centering the robot on its intended path.

### 3. **Completion Phase:**

* The robot transitions to this phase after completing the required number of laps.
  * **Parking Maneuver:** the robot initiates a maneuver to arrive to the parking lot; afterwards, it executes a pre-calculated parking maneuver to conclude the challenge.

---

## 1.5 General Workflow Diagram

Made with Mermaid for GitHub. Visit [Workflow Diagram](./../assets/flowcharts/) folder if the image is distorted or not seen.

```mermaid
graph TD
    %% Nodes
    Start([Start / Power On]) --> Setup[Setup: Init MPU6050, Pixy, Motors]
    Setup --> Calib[Calibrate Gyroscope Offset]
    Calib --> Button{Start Button<br>Pressed?}
    
    Button -- Yes --> ExitPark[Exit Parking Zone]
    ExitPark --> Loop(Start Main Loop ~33Hz)

    subgraph "Navigation & Control Loop"
        Loop --> Sense --> PID[PID Control: Maintain Yaw]
        PID --> ParkMode{Parking Mode<br>Active?<br>}
        
        ParkMode -- Yes --> ParkMan[[Parallel Parking Routine]]
        ParkMan --> End([End Program])
        
        ParkMode -- No --> ColorCheck{Floor Color<br>Detected?}
        
        ColorCheck -- Yes (Blue/Orange) --> TurnLogic[[Corner Turn Routine]]
        TurnLogic --> UpdateLap[Update Lap Count]
        
        ColorCheck -- No --> ObsCheck{Serial read...<br>Obstacle detected?}
        
        ObsCheck -- Yes (R/G) --> EvadeLogic[[Obstacle Evasion Routine]]
        EvadeLogic --> Recenter[Recenter Trajectory]
        Recenter --> Loop
        
        ObsCheck -- No (C) --> Drive[Drive Forward]
        Drive --> Loop
    end

    %% Styling
    style Start fill:#90EE90,stroke:#333,stroke-width:2px,color:black
    style End fill:#FF6961,stroke:#333,stroke-width:2px,color:black
    style Button fill:#FFD700,stroke:#333,stroke-width:2px,color:black
    style Loop fill:#C1E1C1,stroke:#333,stroke-width:2px,color:black
    style ParkMode fill:#FFD700,stroke:#333,stroke-width:2px,color:black
    style ColorCheck fill:#FFD700,stroke:#333,stroke-width:2px,color:black
    style ObsCheck fill:#FFD700,stroke:#333,stroke-width:2px,color:black
    
    style Setup fill:#ADD8E6,stroke:#333,stroke-width:1px,color:black
    style Calib fill:#ADD8E6,stroke:#333,stroke-width:1px,color:black
    style ExitPark fill:#ADD8E6,stroke:#333,stroke-width:1px,color:black
    style Sense fill:#adcae6,stroke:#333,stroke-width:1px,color:black
    style Drive fill:#ADD8E6,stroke:#333,stroke-width:1px,color:black
    style PID fill:#ADD8E6,stroke:#333,stroke-width:1px,color:black
    style UpdateLap fill:#ADD8E6,stroke:#333,stroke-width:2px,color:black
    style Recenter fill:#FF6961,stroke:#333,stroke-width:2px,color:black
    
    style ParkMan fill:#C1E1C1,stroke:#333,stroke-width:2px,stroke-dasharray: 5 5,color:black
    style TurnLogic fill:#C1E1C1,stroke:#333,stroke-width:2px,stroke-dasharray: 5 5,color:black
    style EvadeLogic fill:#C1E1C1,stroke:#333,stroke-width:2px,stroke-dasharray: 5 5,color:black

```

```mermaid
graph TD
    A[Detect Floor Color] --> B{Is it Lap 0?}
    B -- Yes --> C[Define Direction:<br>Blue=Left, Orange=Right]
    B -- No --> D[Use Pre-defined Direction]
    C & D --> E[Measure Front Distance]
    E --> F{Wall Close?}
    F -- Yes --> G[Tight Maneuver:<br>Back up & Turn]
    F -- No --> H[Open Maneuver:<br>Smooth Turn]
    G & H --> I[Update Target Yaw <br>+/- 90 deg]
    
    %% Styling
    style A fill:#ADD8E6,color:black
    style B fill:#FFD700,color:black
    style C fill:#FF6961,color:black
    style D fill:#C1E1C1,color:black
    style E fill:#ADD8E6,color:black
    style F fill:#FFD700,color:black
    style G fill:#FFB347,color:black
    style H fill:#FFB347,color:black
    style I fill:#90EE90,color:black
```

```mermaid
graph TD
    E_A["Detect Blocks with OpenMV"] --> E_B{"Color?"}
    E_B -- Red --> E_C["Avoid to the RIGHT 'R'"]
    E_B -- Verde --> E_D["Avoid to the LEFT 'G'"]
    E_C --> E_E["Send through serial"]
    E_D --> E_E
    E_E --> E_F["When block exits ROI"]
    E_F --> E_G["Send continue 'C'"]

    %% Styling
    style E_A fill:#ADD8E6,color:black
    style E_C fill:#DC143C,color:black
    style E_D fill:#008000,color:black
    style E_E fill:#FFB347,color:black
    style E_F fill:#ADD8E6,color:black
    style E_G fill:#90EE90,color:black
```
Visit:

[Main Workflow Diagram.png](./../assets/flowcharts/Workflow%20Diagram%20-%20Navigation.png)

[Color and Ultrasonic Workflow Diagram.png](./../assets/flowcharts/Workflow%20Diagram%20-%20Color%20and%20Ultrasonic.png)

[OpenMV Workflow Diagram.png](./../assets/flowcharts/Workflow%20Diagram%20-%20OpenMV.png) 

If the image is distorted or not seen.

[Back to Main README.md Index](../README.md)

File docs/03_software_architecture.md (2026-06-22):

# 3. Software Architecture

This section details VizDrive's software architecture, covering essential **libraries**, an overview of its **modular functionalities**, and the overall **firmware structure**. The code is implemented in **C++** for the Arduino Mega 2560 Pro Embed.

---

## 3.1 Required Libraries

VizDrive uses the following Arduino and Adafruit libraries to enable its functionalities:

* **`Servo.h`**: Standard Arduino library for controlling servo motors, specifically for steering.
* **`Wire.h`**: Facilitates I2C (Inter-Integrated Circuit) communication, used by the MPU6050 and the I2C color sensor.
* **`NewPing.h`**: Dedicated library for ultrasonic sensors, optimizing distance measurements.
* **`Adafruit_MPU6050.h`**: Provides the interface for the MPU6050 gyroscope and accelerometer.
* **`Adafruit_Sensor.h`**: A core library supporting various Adafruit sensors, including the MPU6050.
* **`Adafruit_TCS34725.h`**: Integrates the TCS3472 I2C color sensor (this library is compatible with both TCS3472 and TCS34725 color sensor).
* **`Pixy2.h`**: Enables communication and data retrieval from the PixyCam 2.1. (V3 and older)

---

## 3.2 Modular Functionalities

The firmware is structured into independent modules, each abstracting a primary robot function. This modular design improves readability, simplifies debugging, and supports isolated development of specific code sections.

This document provides an **overview** of each module. We highly recommend referring to each module's dedicated documentation for a comprehensive explanation of functionalities.

### Motion and Steering

This module directs the robot's physical movement, including propulsion and directional control.

* **`driveForward(speed)`**: PWM-controlled function for DC motor operation, setting speed as a PWM value (0-255).
* **`driveBackward(speed)`**: PWM-controlled function for DC motor operation, setting speed as a PWM value (0-255) to move the robot in reverse.
* **`stopMotors()`**: Implements a "soft stop" by disabling motor PWM signals, allowing for natural deceleration.
* **`stopBrake()`**: Executes a "hard stop" using short-circuit braking for immediate halts.
* **`setSteeringAngle(angle)`**: Adjusts the front-wheel steering servo position. Angle values are bounded by `SERVO_LEFT` and `SERVO_RIGHT` constants to prevent mechanical interference.
* **`performParking()`**: Manages the precise reverse maneuver required for parking, utilizing encoder pulse count for distance control.
* **`encoderISR()`**: An Interrupt Service Routine (ISR) that increments an internal counter (`encoderPulseCount`) for accurate distance tracking.

**Key Constants:**

* `SERVO_LEFT`, `SERVO_RIGHT`: Define the minimum and maximum safe steering angles.
* `MOTOR_INA_PWM`, `MOTOR_INB_PWM`: Specify the PWM pins for controlling the H-bridge motor driver.
* `PARKING_PULSES`: The calibrated encoder pulse count for the parking distance.

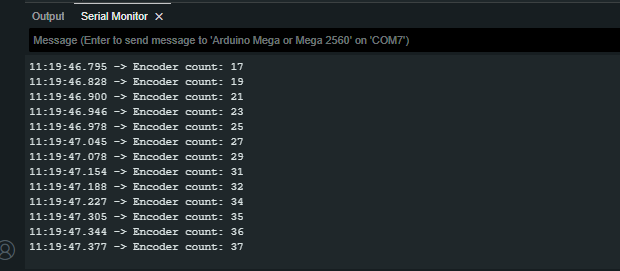
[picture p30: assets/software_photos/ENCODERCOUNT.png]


For detailed explanations of these functions, refer to [**Robot Mobility**](./05_robot_mobility.md).

---

### Distance Detection

This module employs ultrasonic sensors to measure real-time distances to surrounding environmental features, primarily for maintaining optimal positioning relative to walls.

* **`getDistance(sonar)`**: Calculates and filters distance measurements using a `NewPing` object. It performs multiple pings and applies a median-based filtering process to reduce noise and improve accuracy, considering only stable and valid readings within a defined range.

* **`avoidWall(correctionAmount)`**: In the **Open Challenge**, this function adjusts the robot’s orientation by modifying its target yaw when the distance to nearby walls falls outside expected thresholds. It uses the `correctionCooldown()` mechanism to prevent repeated or excessive corrections. The correction thresholds are tuned to keep the robot aligned near the outer wall, allowing adaptability to various center-wall configurations.
  
* **`recentreIfNeeded`**: During the **Obstacle Challenge**, this function sets the servo steering angle to recentre the robot into its intended trajectory. It considers the last detected PixyCam color signature to decide which ultrasonic sensor to use for re-centering, to distinguish between obstacles and walls.

* **`correctionCooldown()`**: Controls the cooldown period for wall corrections. In the **Open Challenge**, it resets the `correctionState` flag after a fixed interval (`correctionCooldownMillis`, typically 1200 ms), enabling new corrections. In the **Obstacle Challenge**, the cooldown resets after every turn, ensuring that only one correction is made after each obstacle avoidance, to avoid misalignment caused by unnecessary adjustments.

* **`avoidWallPID()`**: This function is used in the **Open Challenge** and is designed to keep the robot at a stable and constant distance from the wall while moving forward. It applies a PID-based lateral correction to adjust the robot’s target yaw (heading), preventing it from drifting too close to or too far from the outer wall.

    **Tuning Parameters:**

    * `S_Kp = 0.5;`: Proportional gain, influencing the response to the current heading error.
    * `S_Kd = 0.8;`: Derivative gain, influencing the response to the rate of change of the heading error, helping to dampen oscillations.
    * `S_Ki = 0.0;`: Integral gain, unused, but could be implemented to eliminate steady-state errors.



For a more detailed analysis of the ultrasonic sensors integration for each challenge and the noise filtering function, refer to 
[**Ultrasonic Distance Sensing**](./08_ultrasonic_distance_sensing.md).

---

### Artificial Vision Obstacle Evasion

VizDrive used the **PixyCam 2.1**, now powered by the **OpenMV H7 Plus** to detect and react to colored obstacles in its path.

* **`obstacleDetected()`**: Determines whether an obstacle is within close proximity, based on its position in the camera's frame. Returns `true` if an object is found within a predefined vertical threshold, `false` otherwise.
* **`handleEvasion()`**: Executes a blocking maneuver to steer the robot around an obstacle detected within close range. It identifies the largest obstacle within the ROI and adjusts the robot's steering based on the object's color signature:
    * **Signature 1 (Red)**: Triggers an evasion maneuver to the **right**.
    * **Signature 2 (Green)**: Triggers an evasion maneuver to the **left**.

The function tracks the X-coordinate of the obstacle, and only considers the evasion maneuver complete if the obstacle is detected out of the robot's central path, according to the color signature (e.g., red to the left side, or green to the right side).

**Debugging (Pixy Only):**

* **`debugPixy()`**: Provides serial output of all detected blocks, including their coordinates and signatures. This function is typically commented out in optimized code to conserve processing power but was used during calibration and troubleshooting.



For a comprehensive explanation of PixyCam 2.1 integration, OpenMV H7 plus integration, and computer vision principles, consult [**Computer Vision Functions**](./07_computer_vision.md).

---

### Color Detection

This module is responsible for identifying specific color patterns in the track, crucial for autonomous navigation and turns.

#### 1. Floor Detection (I2C TCS3472 Sensor)

This sensor, mounted underneath the robot, detects navigation cues on the track.

* **Blue**: Indicates a requirement for a **left** turn.
* **Orange**: Indicates a requirement for a **right** turn.
* **`detectFloorColor()`**: Reads raw RGB data from the sensor and normalizes these readings using the clear channel value (`c`) to compensate for ambient light variations. It then compares normalized values against predefined color thresholds to identify the floor color. Importantly, during the robot's **first lap**, this function defines the `direction` variable: **-1 for counter-clockwise** (if blue is detected) and **+1 for clockwise** (if orange is detected).
* **`handleColorAction()`**: Manages the robot's actions when a floor color is detected and no turn is currently in progress. It increments `lapTurnCount`, turns on an LED for visualization, and calculates the `turnTargetYaw` for a 90-degree turn based on the `direction`. It also sets `turningInProgress` to `true` to prevent re-triggering and increases `motorSpeed` to `250` for the turn. During the first lap turn, it includes a `safeDelay(500)` for initial adjustment.

#### 2. Wall Detection (Dual TCS3200 Sensors) (Removed in ViZio 2.0)

Two digital TCS3200 sensors, positioned on the robot's sides, are used primarily for detecting the parking trigger.

* **Magenta**: Detected after completing a specific number of laps (e.g., 4 laps), signaling the parking zone.
* **`detectWallMagenta()`**: Reads filtered RGB values from the appropriate side sensor (selected based on the current turning `direction`) and compares them against magenta-specific thresholds.

**Thresholds:**

* All color detection relies on **empirically tuned** RGB intensity thresholds (0-255) for accurate color identification under varying conditions.



For an in-depth explanation of color sensor operation, calibration, and detection logic, refer to [**Color Detection Functions**](./09_color_detection.md).

---

### Orientation Control

This module ensures the robot maintains a stable trajectory and executes precise turns using an MPU6050 gyroscope and a Proportional-Derivative (PD) control loop.

* The **MPU6050 gyroscope** provides angular velocity data (specifically from its Z-axis) which is integrated to track the robot's current yaw angle.
* **`updateOrientation(dt)`**: The time differential in this function is managed differently according to the challenge round. However, in general, it accumulates the robot's `yaw` angle by integrating the calibrated angular velocity (`gyroZ_deg`) over time (`dt`). And incorporates a `0.1` degree/second noise threshold.
* **`keepOrientation()`**: Implements the PD controller. It calculates an `error` between the `targetYaw` and the current `yaw`, then applies a proportional (`Kp`) and derivative (`Kd`) correction to the steering servo angle (`SERVO_STRAIGHT - (int)(Kp * error + Kd * derivative)`) to guide the robot back to its target heading.
* **`setTargetYaw(angle_deg)`**: Dynamically defines the desired yaw angle for the robot to maintain or achieve during maneuvers (e.g., setting a 90-degree turn target).
* **`getCurrentYaw()`**: Returns the current accumulated `yaw` angle of the robot.
* **`getAbsoluteYawError()`**: Calculates and returns the absolute difference between the `targetYaw` and the current `yaw`, used to determine if a turn has been completed.
* **`completedTurn()`**: Checks if a turn is `turningInProgress` and if the `getAbsoluteYawError()` is below the `TURN_THRESHOLD`. If so, it signifies turn completion, turns off an LED, resets `turningInProgress` and `correctionState`. In the Open Challenge, it reduces `motorSpeed` to `160` for subsequent color detection.
* **Gyroscope Calibration**: An initial calibration routine at setup compensates for any inherent bias or drift in the MPU6050's Z-axis gyroscope readings by averaging `samples` (250) readings to determine `gyroZ_offset`.

**Tuning Parameters:**

* `Kp = 1.8`: Proportional gain, influencing the response to the current heading error.
* `Kd = 1.2`: Derivative gain, influencing the response to the rate of change of the heading error, helping to dampen oscillations.
* `Ki = 0.0`: Integral gain, unused, but could be implemented to eliminate steady-state errors.



For a detailed exploration of MPU6050 integration, calibration, and the PD control algorithm (explaining the exclusion of the integral term), consult [**PID Control for the Gyroscope**](./06_pid_gyroscope_control.md).

---

## 3.3 Program Flow and State Management

The `main.ino` file orchestrates the robot's behavior, with the `setup()` function initializing the system and the `loop()` function continuously managing operational states and transitions.

### Initialization (`setup()`)

The `setup()` function executes once at program startup:

1.  **Serial Communication**: Initiates `Serial.begin(115200)` for debugging and monitoring (matching PixyCam's requirement).
2.  **Module Initialization**: Calls initialization for all hardware and software modules:
    * `initMovement()`: Configures motors, servo, and encoder.
    * `initOrientation()`: Initializes MPU6050 and performs gyroscope calibration.
    * `initVision()`: Prepares the PixyCam for operation.
    * `initUltrasonic()`: Sets up ultrasonic distance sensors.
    * `initColorSensors()`: Initializes both I2C and digital color sensors.
    * `initStateLogic()`: Establishes initial state variables, including `direction` and `targetYaw`.
3.  **Start Condition**: Enters a waiting loop (`waitForStartButton()`) until a physical button press signals the start of autonomous operations. A LED (`ledPin`) illuminates while waiting.
4.  **Timing Baseline**: Records `lastUpdateTime` using `millis()` to establish a timestamp for loop timing.

### Main Loop (`loop()`)

The `loop()` function runs continuously, performing core functionalities in a timed sequence:

1.  **Timing Control**: Ensures that main loop updates occur approximately every 30 milliseconds (roughly 33 Hz), calculating `dt` (delta time) for precise orientation updates, and updating `lastUpdateTime`.
2.  **Continuous Movement**: `driveForward(motorSpeed)` maintains the robot's forward progression.
3.  **Orientation Correction**:
    * `updateOrientation(dt)`: Regularly updates the robot's `yaw` angle.
    * `keepOrientation()`: Applies the PD control logic to adjust steering, maintaining the `targetYaw`.
    * `avoidWall(avoidance_amount)` (Open Round): Realigns the robot relative to the walls using ultrasonic sensors. It is triggered only in emergency situations, specifically when the robot risks collision, with `avoidance_amount` (8 degrees) specifying the correction.
    * `correctionCooldown()`: Manages the time between `avoidWall()` executions.
    * `avoidWallPID()`: (Open Round): Realigns the robot relative to the walls using ultrasonic sensors, with `avoidance_amount` (8 degrees) specifying the correction.
4.  **Obstacle Management (Challenge Round)**:
    * `if (obstacleDetected())`: Checks for obstacles using the PixyCam.
    * `handleEvasion()`: Executes the evasion maneuver if an obstacle is found.
5.  **Color-Based Action**:
    * `if (detectFloorColor())`: Checks for relevant color signals (floor lines).
    * `handleColorAction()`: Manages specific actions such as track turns, determined by the detected floor color.
6.  **Progress State & Shutdown**:
    * `if (turningInProgress)`: Checks the turning in progress flag. If there is a turn in progress, executes the `completedTurn()` function.
    * `completedTurn()`: Checks for the absolute yaw error; if it is below the `TURN_THRESHOLD`, it considers a turn completed.
    * `checkForShutdown()`: Monitors the `lapTurnCount` value; if the required number of laps are completed, the robot waits to arrive to the defined stopping area and halts all operations.

---

## 3.4 State Variables and Logic

The robot's dynamic operational state is managed through a set of global boolean and integer flags:

### State Variables

| Variable | Type | Purpose |
| :--- | :--- | :--- |
| `direction` | `int` | Defines the turning direction: -1 = counter-clockwise (left), +1 = clockwise (right). It's set during the first turn by `detectFloorColor()`. |
| `lapTurnCount` | `unsigned int` | Counts the number of turns completed in the current lap. A full lap is defined as having 4 turns. | |
| `SystemShutdown`  | `bool` | When set to `true`, this flag triggers `checkForShutdown()`, which forcefully stops the motors (`stopBrake()`) and enters an infinite loop, effectively halting all robot activity. |
| `turningInProgress` | `bool` | Prevents re-triggering a turn while one is actively being executed. It is set to `true` upon floor color detection and turn initiation, and `false` when `getAbsoluteYawError()` is within `TURN_THRESHOLD`, signaling turn completion. |
| `correctionState` | `bool` | Flag used to manage a cooldown or limit for ultrasonic corrections. It's set to `true` after an `avoidWall()` correction and reset to `false` by `correctionCooldown()` after a delay in the **Open Round**. It is reset after every completed turn in the **Obstacle Challenge**. |
| `lastCorrectionTime` | `unsigned long` | Stores the `millis()` timestamp of the last wall correction, used by `correctionCooldown()` to manage the cooldown period. |
| `turnTargetYaw` | `float` | Stores the yaw angle the robot aims to achieve during a turn, calculated as `(currentYaw + 90.0 * -direction)`. |
| `targetYaw` | `float` | The desired yaw angle for the robot to maintain, actively corrected by the `keepOrientation()` PID loop. |
| `lastUpdateOrientationTime` | `unsigned long` | In the Obstacle Challenge Round, the `updateOrientation()` function does not require to be given the time differential, it stores and calculates it with the `lastUpdateOrientationTime` variable. |

---

## 3.5 Non-Blocking Delay (`void safeDelay(unsigned long ms)`)

* **Purpose**: Provides a mechanism for pausing execution for a specified duration (`ms`) without completely freezing the robot's critical sensor updates and control logic.
* **Parameters**:
    * `ms`: The duration of the delay in milliseconds.
* **Operation**: Unlike a standard `delay()`, `safeDelay()` continuously executes essential functions such as `updateOrientation()`, `detectFloorColor()`, and `handleColorAction()` within its loop, depending on the delay type. Encoder delays are also used to wait until a specific amount of pulses are detected. This ensures the robot remains responsive to environmental changes even during brief pauses in its main sequence. It still is a blocking delay; however, executes the necessary functions for the robot's adaptability.
  
| Type | Measuring System | Function |
|:----|:----:|----|
|`safeDelay(unsigned long ms)`| Time | Keeps track of orientation. |
|`safeDelayColor(unsigned long ms)`| Time | Keeps track of orientation and allows corner turns to be executed. |
|`encoderDelay(unsigned long cm)`| Distance | Keeps track of orientation. |
|`encoderDelayOrientation()`| Distance | Updates orientation and executes the PID steering system. |
|`safeDelayEvasionEncoder()` (Unused on newer versions) | Distance | Allows obstacle evasion during the delay. |

---

## 3.6 Code Organization

The provided source code is organized into distinct modules (e.g., `main.ino`, `color_detection.cpp`, `movement.cpp`). While presented as a single integrated file for this documentation, in a larger development environment, these would typically be in separate `.cpp` and `.h` files within a `src/` directory. This separation improves code modularity, maintainability, and readability.

---

[Back to Main README.md Index](../README.md)

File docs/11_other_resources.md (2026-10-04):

# 11. Other Resources

This section provides links to supplementary materials, diagrams, and other relevant resources that offer further insight into the VizDrive robot's design, construction, and operation.

This document is primarily intended to serve as a **user manual**, with the set of instructions to build, calibrate, and operate our robot.

## 11.0 Building Instructions

This section is a text description on ViZio´s construction process. There are four main steps: Printing, Assembling, Circuits, and Software.

### Step 1 - Print 3D models

**Overview of recommended settings:** 
* Infill Type: **Honeycomb**
* Infill Density: **20% (lightest) - 40% (best durability)**
* Layer Height: **0.28mm**

**More Information:**
* [Find the models](#111-3d-models)
* [More Details](10_3d_modeling.md)

### Step 2 - Assemble

#### 2.1 Assemble Wheels

  

**Please note:** Front Screws and Rims are not symmetrical, notice there are left and right 3D models

#### 2.2 Assemble Chassis

  

**Components in previous picture:** Nose Cone, M3 Screws, Axle Holder.

#### 2.3 Assemble Rear Drive System

  

  

#### 2.4 Assemble Encoder

  

#### 2.4 Secure Motor and Install Encoder

  

  

#### 2.6 Build Front Axle

  

#### 2.7 Place Rear Electronics

**Parts:** 2x rear ultrasonic, PCB, Mega2560, Mega2560 Plaftorm.

  

#### 2.7 Place Rear Electronics

**Parts:** Front ultrasonic, floor color sensor, OpenMV.

  

#### 2.7 Place Batteries

**Parts:** 9V batteries, 2x 4.2V/3.7V batteries.

  

### Step 3 - PCB

We provide two options for this process: manually soldering the PCB, or fabricating it with a PCB supplier. Find the [circuit diagram or PCB files](#112-components-and-wiring).

### Step 4 - Software

**Required Apps:**

* **[Arduino IDE](https://www.arduino.cc/en/software)**  
  Required for writing, compiling, and uploading C++ firmware to microcontrollers.
* **[OpenMV IDE](https://openmv.io/pages/download)**  
  Required for scripting, camera sensor configuration, and vision processing on OpenMV microcontrollers.

Install these libraries via the **Arduino Library Manager** (`Sketch` ➔ `Include Library` ➔ `Manage Libraries...`) or download them directly using the links below:

| Header File | Library Name | Description / Function | Source Link |
| :--- | :--- | :--- | :--- |
| `<Wire.h>` | **Wire** *(Built-in)* | I2C communication interface for onboard sensors and peripherals. | *Built-in with Arduino Core* |
| `<Adafruit_MPU6050.h>` | **Adafruit MPU6050** | Driver for the MPU-6050 6-axis accelerometer and gyroscope module. | [GitHub Repository](https://github.com/adafruit/Adafruit_MPU6050) |
| `<Adafruit_Sensor.h>` | **Adafruit Unified Sensor** | Base unified sensor hardware abstraction layer required by Adafruit drivers. | [GitHub Repository](https://github.com/adafruit/Adafruit_Sensor) |
| `<Adafruit_TCS34725.h>` | **Adafruit TCS34725** | Driver for the TCS34725 RGB color sensor. | [GitHub Repository](https://github.com/adafruit/Adafruit_TCS34725) |
| `<Servo.h>` | **Servo** *(Built-in)* | Standard servo motor control library for pulse-width modulation (PWM). | *Built-in with Arduino Core* |
| `<NewPing.h>` | **NewPing** | Optimized library for ultrasonic distance sensors (HC-SR04, SRF05, etc.). | [GitHub Repository](https://github.com/teckel12/arduino-new-ping) |

**Code:**

[Download the code here](./../src/)

**Arduino Upload**: 
  * **Source**: Upload the code directly from the Arduino IDE.
  * **Target:** Upload to the Mega 2560 internal storage. *(board name inside IDE: Arduino Mega 2560)*.

**OpenMV Upload**:
  * **Source**: Upload the code directly from the OpenMV IDE. 
  * **Target:** Upload either to an external micro SSD and plug it inside the camera or upload into built-in memory.

## 11.1 3D Models

All custom mechanical parts designed for VizDrive are available as STL files. 
These models can be used for replication, modification, or further study of the robot's physical structure.

* **Chassis:** The main structural frame of the robot.
  * [View 3D Model (STL)](./../models/chassis/chassis.stl)
  * [View Updated 3D Model (STL)](./../models/chassis/chassis2.0.stl)
  * [View International 3D Model (STL)](./../models/chassis/ViZioInternationalMotorFix.stl)
  * [View 2026 Models (STL)](./10_3d_modeling.md#chassis)
* **Front Wheel Rims:** Custom-designed rims for the front wheels.
  * [View 3D Model (STL)](./../models/wheels/wheel_rims.stl)
* **Front Wheel Hubs with Screws:** Hubs connecting to the steering rod, including screw designs.
  * [View 3D Model (STL)](./../models/wheels/wheel_hub.stl)
* **Encoder Wheel and Rear Wheel:** Precision-designed wheel with encoder markings and standard rear wheel.
  * [View 3D Model (STL)](./../models/wheels/encoder_wheel.stl)
* **Steering Rods and Camera Support:** Components for steering rods and the PixyCam mount.
  * [View 3D Model (STL)](./../models/steering/steering_rods.stl)

For the 3D printing guide, visit the [3D Modeling](./10_3d_modeling.md) document. It explains all the parameters and configuration we used for the Creality Ender 3 3D printer.

You can also visualize the **Unity simulator** we created during the modeling process prior to the fabrication of the robot, which is available as a GitHub pages hosted web embed here: [Unity Simulator](.././embeds/Unity_simulator/README.md). Click on the image to access the **Unity web player**.

Unity Simulator Web Player

## 11.2 Components and Wiring

For the construction of our robot, we tried to utilize the most accessible sensors and actuators. Most of them are typically found in standard Arduino kits.

To get the list of all components, refer to the [**Hardware Components**](02_hardware_components.md) document. Which also details on their specifications and utilization.
And for a look into the pin configuration and interface, refer to the [**Sensors and Pin Configuration**](04_sensors_and_pin_configuration.md) document.

For the wiring, we created a custom PCB design. All the connections are traced in the **Electromechanical Diagram** made with Cirkit.
Which also has an [**interactive web design**](https://vd-wro.github.io/VD26/embeds/interactive_circuit), created with an HTML embed. It also includes a ChatBot that could help you to understand the general operation of the circuit and its components' connection.

Electromechanical Diagram

We've also created a custom KiCad PCB to improve durability, reliability and simplicity. You can acces the files in [kicad_pcb](../src/kicad_pcb).

## 11.3 Building Guides

### Video Resources

We created 3D animations that showcase the detailed building instructions for all the components into our robot. The videos also include information about the different versions of the robot.

For an in-depth explanation into this and other concepts taken into consideration during the planification of 3D parts, you can visit the [3D Modeling](./10_3d_modeling.md) document, which details the principles used during the construction of our robot.

Building Instructions (https://www.youtube.com/watch?v=Cte4G7Wkx94)

ViZio 2.0 (https://www.youtube.com/watch?v=JOWvUNmzN1w)

ViZio V3 (https://www.youtube.com/watch?v=J1BOTFqHlQ4)

ViZio IV (https://www.youtube.com/watch?v=X2UGbEu-D34)

ViZio IV (https://www.youtube.com/watch?v=UHFCzMF-fk8)

### 3D Viewer

Take a better look at ViZio by visiting this interactive robot viewer!

### [Interactive Robot Viewer](https://vd-wro.github.io/VD26/embeds/Robot)

## 11.4 Sensors' Calibration

### MPU-6050 Gyroscope + Accelerometer

The **MPU-6050** was calibrated by calculating the offset through averaging a specific number of samples. The empirical data collected during MPU calibration, demonstrating the reduction in accumulated error as the number of samples increases, can be visualized in the graph below.

Calibration Data Graph (PNG)

This **Accumulated Error vs. Number of Samples** graph indicates that 250 samples are sufficient to achieve an accuracy of 
±0.01 in our sensor model. However, this may vary depending on the specific gyroscope and accelerometer model.

We provide our calibration code, which calculates the offset accumulation of the MPU-6050 over a defined period, making the necessary data analysis for calibration easily accessible. When using this code, ensure the MPU-6050 remains static.

For more information on MPU-6050 orientation control, please refer to the [**PID Gyroscope Control**](06_pid_gyroscope_control.md) document.

### HC-SR04 Ultrasonic Sensor

The HC-SR04 ultrasonic sensor required an algorithm to mitigate noise and ensure more accurate measurements. We developed a custom median and outlier filter for this purpose. The **Raw vs. Filtered Ultrasonic Measurement Graph** illustrates the difference between the raw and filtered ultrasonic measurements.

View Filter Data Graph (PNG)

It is crucial to evaluate the optimal number of samples for the filter to maintain consistent measurements without impacting performance. We highly recommend using **5 samples** for the filter, but also provide the [**ultrasonic sensor median filter code**](.././src/ultrasonic_median_filter/ultrasonic_median_filter.ino) if you want to visualize your own data.

For more information on HC-SR04 ultrasonic measurement and filter, please refer to the [**Ultrasonic Sensing**](08_ultrasonic_distance_sensing.md) document.

## 11.5 PID Control Parameters

The PID Control parameters are empirically tuned following the next set of steps:

* **Kp (Proportional Gain)**: is adjusted by gradually increasing it until the robot starts oscillating around the desired path (indicating overcorrection), then slightly reducing it to achieve a balanced response.
* **Kd (Derivative Gain)**: is tuned after Kp to smooth the response, reduce overshoot, and dampen oscillations, leading to a more precise and stable trajectory.
* **Ki (Integral Gain)**: is used to correct accumulative errors. It is not implemented in the code due to over-correction and wind-up (more information on this topic).

We highly recommend visiting our documentation on this topic, to understand the PID control parameters adjustment and the **Ki parameter** exclusion [**PID Gyroscope Control**](06_pid_gyroscope_control.md)

## 11.6 Code Structure

The most recent and complete version of our code is located in the `./src/main_control` folder. This code is optimally organized into various modules with `.cpp` and `.h` files, alongside a `main.ino` file. However, for presentation and readability, it's provided as a single, functional code.

While code modularity is an optional step for more sophisticated and larger systems, for simplicity, the different sections are clearly separated by comments within the code itself.
For more information, refer to our documentation on the [**Software Architecture**](03_software_architecture.md).

## 11.7 Technical Issues and Implemented Remedies

* **Safe Delay Looping**: This was one of the toughest problems we faced. The robot looped during the `safeDelay()` functions infinitely. Initially we thought it was a `millis()` or `micros()` saturation problem, but this was not the root cause of the problem. After debugging we found out the MPU stopped working arbitrarily, which froze the `safeDelay()` functions that used `updateOrientation()`. Two things were implemented for the solution:
  * First, a `micros()` control was used to update MPU values with a controlled frequency. This reduced the casualties of looping but did not fully eliminate the problem.
  * Secondly, a `Wire.setWireTimeout(3000, true)` to reset the bus anytime no I2C information was received from the gyroscope, this allowed the bus to restart and keep receiving orientation data after it freezes.

* **Wheel Encoder Paint**: It’s important to paint the encoder wheel as shown in [**3D Modeling**](./10_3d_modeling.md) to ensure proper operation of the light-based encoder. Otherwise, light may pass through the thin plastic layer.

* **Ultrasonic Sensors**: Before installation, it’s needed to carefully straighten the ultrasonic sensor pins with pliers. When sliding the sensor into its friction-fit mount, only the left and right units should be secured with wire to ensure proper alignment and operation.

* **Pixy Calibration**: It’s crucial to cover the Pixy’s lens with your finger during initialization to calibrate its brightness and avoid variable exposition due to slight lighting changes during power-up.

---

If you notice any inconsistency on this code functionality, feel free to contact us via email: **<vizdrive.wro@gmail.com>**!
Of course, we are also open to any recommendation, inquiry or comment on any topic.

[Back to Main README.md Index](../README.md)

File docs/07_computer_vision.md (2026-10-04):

# 7. Vision and Distance Sensing

VizDrive now utilizes the OpenMV H7 Plus to detect and react to obstacles in real time.

---

## 7.1 OpenMV H7 Plus
The **OpenMV Cam** is a small, low power, microcontroller board uses machine vision in the real-world. For this instance, we are using blob based color detection, using LAB color space.

### Camera Configuration

Overview of the camera's setup and code.

#### Sensor and System Initialization

All required libraries are imported, serial communication to the Mega is established through `UART3` (OpenMV) and `SERIAL1` (Mega). LEDs in the camera are defined, for they are used as block detection indicators for easier debugging. Pixel format and frame size are set up for optimal LAB blob detection.

```py
from pyb import UART, LED
import sensor, image, time, mjpeg

# Parabolic calculation
y_threshold = 119 * 0.60

# ====================== Peripherals ======================
# Initialize serial communication (UART)
# UART 3 at 115200 bps for communication.
uart = UART(3, 115200)

# Initialize on-board status indicators
red_led = LED(1)
green_led = LED(2)

# ====================== Camera Config ======================
# Reset and initialize the camera sensor hardware
sensor.reset()
# Configure pixel format to RGB565 (16-bit per pixel, Red-Green-Blue)
sensor.set_pixformat(sensor.RGB565)
# Configure frame size to QQVGA (Quarter Quarter Video Graphics Array: 160x120 pixels)
sensor.set_framesize(sensor.QQVGA) # res: 160x120

# - Parameter blocking -
# Disable Automatic Gain Control (AGC) to ensure deterministic color evaluation
sensor.set_auto_gain(False)

# Disable Automatic White Balance (AWB) and lock precise digital RGB gains 
# to maintain color consistency across variable environmental illumination
sensor.set_auto_whitebal(False, rgb_gain_db=[40.0, 38.0, 40.0])

# Disable Automatic Exposure Control (AEC) and set static exposure 
sensor.set_auto_exposure(False, exposure_us=50000)

# Allow sensor clock and automatic adjustments to stabilize over a 2000ms window
sensor.skip_frames(time=2000)

# Initialize the frame rate tracking clock
clock = time.clock()
```

Functions like AWB (auto-white-balance), auto-gain, and auto-exposure are disabled to maintain stable lighting during the whole trajectory. Start-up AWB gain overwrite and auto-gain coefficients are configured to a specific value, attempting to achieve similar conditions every time the camera boots; it is not possible to initialize the camera without a start-up AWB, gain, and exposure. For this white balance configuration specifically, red and blue gains are incremented, it balances out the initial start-up AWB. This balance is required since the robot starts with the magenta wall in front, and it is necessary to boost these values to achieve a clean white balance.

#### Color Detection Functions and Initialization

Main color thresholds are established for red and green blobs using LAB color space. Even though magenta contains slightly more blue than red, it is still a minimal difference to distinguish the parking lot from the red obstacles, so, for red specifically, an additional hue factor was included into the filtering to verify it is true red, and not magenta.

```py
# COLOR THRESHOLDS (CIE L*a*b* COLOR SPACE)
# Red Threshold:
red_threshold = (10, 90, 17, 127, 21, 120)
# Hue boundaries for red chrominance validation
RED_H_MIN = 0
RED_H_MAX = 20

# Green Threshold:
green_threshold = (10, 91, -128, -12, -35, 40)

uart.write("a") #======================== SETUP FINISHED - Confirm Message

# Validates whether a detected blob conforms to true red chrominance criteria by converting its centroid pixel to the HSV color space.
def is_true_red(img, blob):
    # Sample the RGB values directly from the centroid coordinates of the blob
    r, g, b = img.get_pixel(blob.cx(), blob.cy())

    # Normalize standard 8-bit integer RGB values to floating-point values between 0.0 and 1.0
    r_n, g_n, b_n = r / 255.0, g / 255.0, b / 255.0
    mx = max(r_n, g_n, b_n)
    mn = min(r_n, g_n, b_n)
    df = mx - mn

    # Compute Hue (H) based on the dominant primary color channel
    if mx == mn:
        h = 0
    elif mx == r_n:
        h = (60 * ((g_n - b_n) / df) + 360) % 360
    elif mx == g_n:
        h = (60 * ((b_n - r_n) / df) + 120) % 360
    elif mx == b_n:
        h = (60 * ((r_n - g_n) / df) + 240) % 360

    # Downscale the standard 360-degree Hue circle to an 8-bit compliant 0-179 range
    h_scaled = int(h / 2) 

    # Evaluate the scaled hue against the predefined upper boundary constraint
    return (h_scaled <= RED_H_MAX)
```

#### Anti-Jittering

To eliminate single-frame detection noise caused by camera shake or lighting shifts, this function uses a 3-frame rolling window. It returns the majority state across the sample count.

state_history = ['C', 'C', 'C']

```py
def update_and_get_filtered_state(new_state):
    # Displace history and add new data
    state_history.pop(0)
    state_history.append(new_state)
    
    # Votation for majority: if 'R' or 'G' appear 2 o or more times, send true; else, 'C'.
    if state_history.count('R') > 1:
        return 'R'
    elif state_history.count('G') > 1:
        return 'G'
    else:
        return 'C'
```

#### Blob Detection and Y-Bound Filter

This is the main loop, it reads the sensor information and runs two separate blob detection functions, this is due to the limitations of a single function performing two readings at the same time: if both blobs are together, or overlap, none are returned from the function, so the two-function approach was chosen. The only difference between the red and green function is in the hue factor, which is only applied to the red blob detection function. For all blobs inside the sensor frame, only the ones inside the Y-bound ROI are taken into consideration, and elected as **candidates**.

```py
while True:
    # Update internal frame rate monitor clock
    clock.tick()
    
    # Capture the latest image frame from the sensor
    img = sensor.snapshot()

    # Isolate pixel clusters aligning with defined red and green color matrices
    red_blobs = img.find_blobs([red_threshold], pixels_threshold=100, area_threshold=100)
    green_blobs = img.find_blobs([green_threshold], pixels_threshold=100, area_threshold=100)

    # Initialize list to filter and collect candidate targets
    candidates = []

    # Apply y_filter only if required
    for blob in red_blobs:
        if is_true_red(img, blob):
            if not apply_y_filter or blob.cy() > y_threshold:
                candidates.append(("R", blob))

    for blob in green_blobs:
        if not apply_y_filter or blob.cy() > y_threshold:
            candidates.append(("G", blob))

    raw_state = 'C'
    active_blob = None
    active_color = None

    # Default State: Ensure status indicators are darkened prior to target processing
    red_led.off()
    green_led.off()   
```

#### Size Filtering and Data Transmission

This function is inside the main loop, and it filters out the prevously elected candidates, keeping only the one with the largest area. After the final blob is elected, the camera checks if the block is in the safe-zone or in the region of interest, and commands the right maneuver, optimizing the route if possible. The message is then constructed, consisting of a single character, and proceeds to send the message of the classified block through UART Serial communication.

```py
    if len(candidates) > 0: # more than 1 blob is detected
        # Blob with the most area is selected
        color, blob = max(candidates, key=lambda item: item[1].pixels())
        cx, cy = blob.cx(), blob.cy()

        # Checks if maneuver is necessary
        if color == "R":
            if cx < LEFT_SECTION_END_X:
                # Evasion is NOT required - optimize route
                raw_state = 'C'
            else:
                # Evasion is required - evade obstacle
                raw_state = 'R'
                active_blob = blob
                active_color = "R"

        # Checks if maneuver is necessary        
        elif color == "G":
            if cx > RIGHT_SECTION_START_X:
                # Evasion is NOT required - optimize route
                raw_state = 'C'
            else:
                # Evasion is required - evade obstacle
                raw_state = 'G'
                active_blob = blob
                active_color = "G"
 # --- APLICAR FILTRO DE ESTABILIZACIÓN ---
    current_state = update_and_get_filtered_state(raw_state)

    # --- GESTIÓN DE LEDS Y VISUALIZACIÓN SEGÚN ESTADO FILTRADO ---
    red_led.off()
    green_led.off()
        
    # Output runtime diagnostics to the serial debugging terminal
    print("FPS:", clock.fps())
    # Envío de datos por UART al otro microcontrolador
    uart.write("{}\n".format(current_state))
```

#### Debugging

Simple debugging for recording and IDE visualization.

```py
    if current_state == 'R' and active_blob:
        red_led.on()
        img.draw_rectangle(active_blob.rect(), color=(255, 0, 0))
        img.draw_cross(active_blob.cx(), active_blob.cy(), color=(255, 0, 0))
        img.draw_string(active_blob.x(), active_blob.y(), 'R', color=(255, 0, 0))
    elif current_state == 'G' and active_blob:
        green_led.on()
        img.draw_rectangle(active_blob.rect(), color=(0, 255, 0))
        img.draw_cross(active_blob.cx(), active_blob.cy(), color=(0, 255, 0))
        img.draw_string(active_blob.x(), active_blob.y(), 'G', color=(0, 255, 0))
```

### Main Control Configuration

Overview of the Mega's setup and code.

#### Initialization (`void initVision()`)

  * **Purpose**: Establishes serial communication with the OpenMV.
  * **Operation**:
      * `Serial1.begin(115200);`: Initializes serial communication at 115200 baud rate.
      * Waits until the OpenMV is fully initialized, and sends a message `uart.write("a")`.

```cpp
void initVision() {
  Serial1.begin(115200);
  while(!Serial) delay(100);
  while(Serial.available() )
  delay(1000);
  Serial.flush();
  delay(100);
  Serial.println("Artificial vision initialized...");
}
```

#### Obstacle Detection (`void obstacleDetected()`)

  * **Purpose**: Checks if an obstacle classified to be evaded is available.
  * **Operation**:
      * `return (visionComand);`: Sends "true" whenever there is and evasion instruction coming from the camera.

```cpp
// Checks if any part of any detected block is within the crucial lower region (below ROI_Y_BOUND).
bool obstacleDetected() {
  readVision();
  return (visionCommand == 'R' || visionCommand == 'G');
}
```

#### Data Retrieval (`void readVision()`)

  * **Purpose**: Establishes serial communication with the OpenMV.
  * **Operation**:
      * Checks if there is data available `Serial1.available() > 0` and then retrieves the data avaiable `char c = Serial1.read();`.
      * Checks for the single-character data that are true instructions, filtering out possible noise.
      * Assigns the data to `visionCommand` variable.

```cpp
void readVision() {
  while (Serial1.available() > 0) {
    char c = Serial1.read();
    if (c == 'R' || c == 'G' || c == 'D' || c == 'C') {
      visionCommand = c;
    }
  }
}
```

#### Serial Flush (`void clearSerial()`)

  * **Purpose**: Flushes out residue data from the serial buffer.
  * **Operation**:
      * Checks if there is data available `Serial1.available() > 0` and then flushes the data in the buffer `Serial1.read();`.

```cpp
void clearSerial() {
  while (Serial1.available() > 0) {
    Serial1.read(); 
  }
  Serial.println("Serial clear");
}
```

### Obstacle Evasion Logic - OpenMV (`void handleEvasion()`)

#### Initiation and Data Update

After confirming an active obstacle using `obstacleDetected()`, the evasion protocol initializes core variables and enters the main execution loop. On each iteration, the function refreshes the evasion instructions by reading `visionCommand`, updates orientation via `updateOrientation()`, and refreshes floor line data through `detectFloorColor()`. If a colored line is detected, the function executes handleColorAction() and breaks out of the loop to terminate the evasion maneuver.
         
```cpp
  if (!obstacleDetected()) return; // Validates active obstacle

  Serial.println("--- EVASION PROTOCOL INITIATED ---");
  int activeSignature = 0; 

  while (true) {
    readVision(); // Updates 'visionCommand'
    updateOrientation();

    if (detectFloorColor()) {
      handleColorAction();
      break;
    }
```

#### Evasion Maneuver

An `activeSignature` flag is present to execute the function once, optimizing the loop. If no active signature is present, thee cases are possible: evade right, left, or go straight. After setting steering direction, it assigns the block's color to `activeSignature`.

```cpp
    // 1. Assign signatureValue if it is the fist instance of the loop with a block
    if (activeSignature == 0) {
      if (visionCommand == 'R') {
        activeSignature = SIGNATURE_RED;
        setSteeringAngle(SERVO_RIGHT); // Evade red to the right
        Serial.println("Obstacle is RED. Evading RIGHT.");
      } else if (visionCommand == 'G') {
        activeSignature = SIGNATURE_GREEN;
        setSteeringAngle(SERVO_LEFT); // Evade green to the left
        Serial.println("Obstacle is GREEN. Evading LEFT.");
      } else {
        setSteeringAngle(SERVO_STRAIGHT);
        lastSignature = 0;
        Serial.println("Unknown signature. Aborting evasion.");
        break; 
      }
    }
```

#### Finish Evasion

It finishes the evasion maneuver and breaks the evasion applying sideways correction, explained in [**Ultrasonic Distance Sensing**](./08_ultrasonic_distance_sensing.md).

```cpp
    // 2. exit condition calculated inside the OpenMV's logic
    if (visionCommand == 'C') { // Exit Evasion
      
      if (activeSignature == SIGNATURE_RED) {
        if (lastSignature != 0) resetYawCorrection(); // Reset correction if previous correction has been applied
        Serial.println("Evasion successful. Red block is safe.");
        lastSignature = SIGNATURE_RED; // Assign Signature Value
        if (safeDelayColor(400)) break; // If floor line is detected, break

        setSteeringAngle(SERVO_LEFT-5); // Pivoting maneuver, depending on yaw error
        if (getAbsoluteYawError() > 65){ if (safeDelayColor(1200)) break; } 
        else if (getAbsoluteYawError() > 35){ if (safeDelayColor(900)) break; } 
        else { if (safeDelayColor(500)) break; } // If floor line is detected, break
        
        break; 
      } 
    }
```

### Camera Positioning

#### X Axis

**Recentering Maneuver:** A fisheye lens adds complex distortion that hinders accurate object tracking. Our solution to maintain accurate detection when obstacles are off-view was maintaining the default 2.8 mm lens and adding a [recentering maneuver](05_robot_mobility.md).

#### Y Axis

A 10° angle was opted when choosing the optimal camera position, this angle permits the usage of the non-curve area of the camera (horizontal center line) during object tracking. Even though the Y-bound (a value used to detect only blocks that are near the robot, and discard those that are far away) could be assumed to be the centre, it was calculated to create micro adjustments:



**Block Detection Distance Calculations**

**Parameters & Constants:**

* **FOV:** $52^\circ$
* **Y-bound:** $0.40$
* **Camera Height:** $11\text{ cm}$
* **Target Point Height:** $5\text{ cm}$ (center of $10\text{ cm}$ block)

**Calculations:**

1. **Upper FOV Angle:**
   $$52^\circ \cdot 0.40 = 21^\circ \quad \text{(upper part)}$$

2. **Half FOV Angle:**
   $$\frac{52^\circ}{2} = 26^\circ$$

3. **Offset from Center:**
   $$26^\circ - 21^\circ = 5^\circ \quad \text{(offset from center)}$$

4. **Block Detection Distance:**
   $$\text{Block detection distance} = \frac{(11 - 5)\text{ cm}}{\tan(10^\circ - 5^\circ)} \approx 69\text{ cm}$$

## 7.2 PixyCam 2.1 for Vision-Based Obstacle Evasion

The **PixyCam 2.1** is an intelligent, compact vision sensor that provides rapid object recognition based on pre-trained color signatures. Its integrated processor significantly offloads computational burden from the main microcontroller, enabling real-time obstacle detection.

### Global Object and Configuration Parameters

```cpp
Pixy2 pixy; // PixyCam 2.1 object for communication and control

#define SIGNATURE_RED 2   // Defined signature ID for red obstacles
#define SIGNATURE_GREEN 1 // Defined signature ID for green obstacles

/* Configuration of the Region of Interest
   Coordinates of the Pixy resolution: width: 316, height: 208 */

// Y-coordinate threshold for an object to be considered "near" and start evasion.
// Any part of the object below this Y-coordinate will trigger detection.
const int ROI_Y_BOUND = 208 / 6;

const int IMAGE_WIDTH = 316;
// Define sections of the image for evasion completion check
const int LEFT_SECTION_END_X = IMAGE_WIDTH / 3;      // X-coordinate separating left third
const int RIGHT_SECTION_START_X = (2 * IMAGE_WIDTH) / 3; // X-coordinate separating right third
```

### Initialization (`void initVision()`)

  * **Purpose**: Establishes communication with and initializes the PixyCam 2.1 module.
  * **Operation**:
      * `pixy.init();`: Calls the initialization function from the `Pixy2` library. This function configures the SPI interface and prepares the camera for block detection.

### Obstacle Detection (`bool obstacleDetected()`)

  * **Purpose**: Determines if any detected colored object ("block") is currently present within the crucial lower region (below `ROI_Y_BOUND`).
  * **Operation**:
    1.  `pixy.ccc.getBlocks();`: Commands the PixyCam to process the current frame and retrieve a list of detected blocks (objects with assigned color signatures).
    2.  `if (pixy.ccc.numBlocks == 0) return false;`: If no blocks are reported by the PixyCam, no obstacles are present, and the function returns `false`.
    3.  **Iterative ROI Check**: The function then iterates through all detected `pixy.ccc.blocks`. For each block:
          * `if (pixy.ccc.blocks[i].m_y + (pixy.ccc.blocks[i].m_height / 2) > ROI_Y_BOUND)`: Checks if the bottom edge of the block extends beyond the `ROI_Y_BOUND`. If an object is found in this range, it is considered an obstacle, and the function immediately returns `true`.
    4.  If the loop completes without identifying any blocks in the crucial lower region, the function returns `false`.

### Debugging Function (`void debugPixy()`)

  * **Purpose**: Provides detailed real-time information about blocks detected by the PixyCam to the Serial Monitor, aiding in calibration and troubleshooting.
  * **Operation**: It iterates through `pixy.ccc.numBlocks` and prints the index, X/Y coordinates, and color signature of each block. It also explicitly indicates whether each block falls within the defined ROI (`LEFT_BOUND` and `RIGHT_BOUND`). This function is typically commented out in the main code for performance optimization but is invaluable during development.

### PixyMon Configuration and Parameters

The PixyCam 2.1 requires initial setup and color signature training via the **PixyMon** software (compatible with Windows, macOS, and Linux). This graphical interface enables precise calibration of color signatures and adjustment of various camera parameters, which are then saved directly to the PixyCam's firmware.

Here are the key configurations applied in PixyMon for obstacle detection:

| Configuration Area | Parameter / Setting | Value / Description | Image |
| :--- | :--- | :--- | :---: |
| **Program** | `File > Set program` | **`ccc_program`**: This program (Color Connected Components) is selected as it is specifically designed for detecting and tracking color-coded objects. |  |
| **Signatures** | `Action > Set Signature` | **`Signature 1 (Green)`** and **`Signature 2 (Red)`**: These specific signature IDs are assigned to the green and red obstacles on the competition field. Each signature is 'taught' by drawing a bounding box around the target object in the live video feed. |  |
| | `Configure > Signature N` | **Hue, Saturation, Value (HSV) Ranges**: After teaching, these ranges are meticulously fine-tuned for each signature. The goal is to optimize detection reliability under varying ambient light conditions and to minimize false positives from background colors. |  |
| **Camera** | `Configure > Camera` | **Brightness**: Adjusted to an optimal level to ensure good image exposure without over-saturation or underexposure. |  |
| | `Configure > Camera` | **Auto White Balance**: **Enabled (`Auto`)** to allow the camera to automatically adapt to different lighting temperatures on the field, ensuring consistent color interpretation. |  |
| | `Configure > Camera` | **Auto Exposure**: **Enabled (`Auto`)** for automatic adjustment of exposure settings. This is crucial for adapting to dynamically changing light intensities throughout the mission. |  |
| | `Configure > Camera` | **LED Mode**: Set to `Auto` or `On` as needed to ensure proper illumination of detected objects for consistent signature recognition. |  |
| **Interface** | `Configure > Interface` | **Data Out Port**: Set to **`SPI`** to enable high-speed serial communication with the Arduino Mega. |  |
| **Expert** | `Configure > Expert` | **Max Blocks**: Set to a low value (e.g., `2`) to limit the number of reported blocks, focusing on the most dominant obstacles. |  |
| | **Min Block Size (Width/Height)** | Configured to filter out very small (and likely distant or noisy) detections, ensuring only relevant obstacles are reported. |  |
| | **Merge Blocks** | **Enabled**: This setting is activated to instruct the PixyCam to merge adjacent detections of the same color signature into a single, larger block, improving robustness for objects that might be detected as fragmented. |  |

---

Pixymon Software

### Pixy Parameters Decalibration

While we were competing in the Nationals, we noticed something: our robot kept failing to properly evade the objects. Every other logic was working, which led us to know that it was the Pixy which was the problem. 
However, we later found an unsolved **bug** in PixyCam's software; tuning parameters such as AWB (Auto White Balance), auto-exposure, and AWB on start-up did not work, this meant that everytime we started the bot, parameters changed. If you are working, this is what we suggest trying to avoid dramatic changes:

* **Method 1 (Room is well-lit and uniform):** Set `Camera Brightness` to 0, Pixycam will now always initiate with the same brigthness value, this means room lighting needs to be appropriate for proper functioning.
* **Method 2 (Room is slightly dark):** Set `Camera Brightness` anywhere between 1-3, choose what works best for the room. Please note there is a drastic change between `Camera Brightness = 0` and `Camera Brightness = 1`, `Camera Brightness = 1` up until `Camera Brightness = 3` are subtle changes. With this method, we highly recommend to start the bot with your finger over the camera lens so that the brightness value is always as consistent as possible.

Besides the mentioned software problem, the combination of a poor camera sensor and poor AWB worsened the camera brightness problem. It was extremely hard to find the right balance between red and green, green being the much darker color, shown as almost black, compared to the excessively bright red objects.

### Obstacle Evasion Logic - Pixy (`void handleEvasion()`)

  * **Purpose**: Manages the robot's steering to actively evade a detected obstacle, continuing until the path is clear.
  * **Operation**:
    ```cpp
    if (!obstacleDetected()) {
      return;
    }
  
    // --- Start of the blocking evasion loop ---
    // Once this point is reached, the car is committed to evading.
    Serial.println("--- EVASION PROTOCOL INITIATED ---");
  
    int activeSignature = 0; // Stores the signature of the obstacle being evaded (1 for red, 2 for green).
  
    // This loop will now run indefinitely until the exit condition is explicitly met.
    while (true) {
      readBlock(); // old function -> pixy.ccc.getBlocks(); // Get the latest block data in every iteration.
      updateOrientation();
      if (detectFloorColor()) {
        handleColorAction();
        break;
      }
    ```

    1.  **Initial Obstacle Check**: `if (!obstacleDetected()) return;`: The function first verifies the presence of a nearby obstacle. If none is detected, the evasion protocol is not initiated.
    2.  **Continuous Evasion Loop**: Upon detecting an obstacle, the robot enters a `while(true)` loop, committing to the evasion process. This loop ensures the robot continues evasion maneuvers until an explicit exit condition is met.
          * `readBlock();` or `pixy.ccc.getBlocks();`: At the beginning of each loop iteration, updated block information is retrieved.
          * `updateOrientation();`: Ensures the robot's current heading is continuously monitored.
          * `if (detectFloorColor()) { handleColorAction(); break; }`: Allows for an early exit from the evasion loop if a floor color (turn signal) is detected, transitioning back to primary navigation.
    ```cpp
    int selectedIndex = -1;
    int largestArea = 0;
 
    // 2. Find the largest, most relevant obstacle currently in the "near" zone (Pixy only).
    for (int i = 0; i < pixy.ccc.numBlocks; i++) {
      if (pixy.ccc.blocks[i].m_y + (pixy.ccc.blocks[i].m_height / 2) > ROI_Y_BOUND) {
        int area = pixy.ccc.blocks[i].m_width * pixy.ccc.blocks[i].m_height;
        if (area > largestArea) {
          largestArea = area;
          selectedIndex = i;
        }
      }
    }
    ```
    3.  **Largest Relevant Obstacle Selection (Pixy only, OpenMV performs the filtering on-board)**:
          * The function iterates through all detected blocks to find the largest one (based on `width * height`) that is also within the `ROI_Y_BOUND`. This ensures the robot prioritizes reacting to the most prominent obstruction.
    4.  **Maneuver Based on Signature**: If a valid, relevant block is selected:
          * `int currentSignature = currentColor` or `int currentSignature = pixy.ccc.blocks[selectedIndex].m_signature;`: The color signature of the selected block is read.
          * `if (activeSignature == 0)`: This condition ensures that the evasion direction is determined only once at the beginning of the evasion sequence, based on the first detected obstacle's signature.
              * `if (activeSignature == SIGNATURE_RED) { setSteeringAngle(SERVO_RIGHT); lastSignature = SIGNATURE_RED; }`: If the obstacle is `SIGNATURE_RED`, the robot steers to the right.
              * `else if (activeSignature == SIGNATURE_GREEN) { setSteeringAngle(SERVO_LEFT); lastSignature = SIGNATURE_GREEN; }`: If the obstacle is `SIGNATURE_GREEN`, the robot steers to the left.
              * `else { setSteeringAngle(SERVO_STRAIGHT); lastSignature = 0; break; }`: If an unrecognized signature is encountered, the robot attempts to steer straight and exits the evasion loop.
    5.  **Evasion Completion Check**: This is the primary exit condition for the `while` loop. The robot breaks evasion only when the designated obstacle has been successfully navigated past and is located in a "safe" horizontal section of the image.
          * `if (activeSignature == SIGNATURE_RED && currentX < LEFT_SECTION_END_X)`: If a red obstacle was being evaded, and its `currentX` coordinate is now in the leftmost third of the image, evasion is considered complete.
              * A `safeDelayColor(500)` is introduced, followed by `setSteeringAngle(SERVO_LEFT)` with `safeDelayColor()` (the time depends on yaw error) to ensure a full pivot past the obstacle before breaking the loop.
          * `else if (activeSignature == SIGNATURE_GREEN && currentX > RIGHT_SECTION_START_X)`: Similarly, if a green obstacle was being evaded and its `currentX` coordinate is now in the rightmost third of the image, evasion is complete.
              * A `safeDelayColor(600)` is introduced, followed by `setSteeringAngle(SERVO_RIGHT)` with `safeDelayColor()` to ensure a full pivot.
    6.  **Loss of Sight Handling**: If `selectedIndex` remains `-1` (meaning no block is currently detected in the "near" zone), the robot continues to execute the last commanded steering action. This prevents premature termination of the evasion sequence if the camera momentarily loses sight of the obstacle.
    7.  **Evasion Completion**: Once the `while` loop is broken (either by successful evasion or floor color detection), the evasion protocol is considered complete. The robot's steering will typically revert to `SERVO_STRAIGHT` in the subsequent iteration of the main program loop.

  Evasion

[Back to Main README.md Index](./../README.md)

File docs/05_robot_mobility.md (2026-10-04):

# 5. Robot Mobility

This section provides an in-depth analysis of VizDrive's mobility system, covering mechanical design considerations, motor and steering configurations, and the software module responsible for locomotion.

---

## 5.1 Software Mobility Module

The `movement` module contains the core functions that govern VizDrive's locomotion, abstracting motor and steering control.

### Hardware Definitions

The following preprocessor definitions specify the Arduino pins connected to the motor driver, servo, and encoder:

```cpp
#define MOTOR_INA_PWM 4 // PWM pin for motor INA (DC Motor Driver)
#define MOTOR_INB_PWM 5 // PWM pin for motor INB (DC Motor Driver)
#define SERVO_PIN 6     // Pin for the steering servo motor
#define ENCODER_PIN 2   // Digital pin for the quadrature encoder interrupt
```

### Global Variables and Constants

* **`motorSpeed`**: `const int motorSpeed = 150;` (Defined in `main.ino`) - The default PWM value (0-255) for consistent motor speed during standard operations.
* **`steeringServo`**: `Servo steeringServo;` - The object representing the steering servo motor.
* **`encoderPulseCount`**: `volatile unsigned long encoderPulseCount = 0;` - A volatile counter that increments with each pulse from the encoder wheel, tracking distance traveled.

### Steering Angle Constants

These constants define the safe operational range for the steering servo:

```cpp
const int SERVO_STRAIGHT = 85; // Servo angle for straight-ahead motion
const int SERVO_MAX = 35;      // Maximum angular deflection from SERVO_STRAIGHT (maximum steering angle is 45 degrees)
const int SERVO_LEFT = SERVO_STRAIGHT - SERVO_MAX; // Minimum servo angle for extreme left turn (e.g., 50 degrees)
const int SERVO_RIGHT = SERVO_STRAIGHT + SERVO_MAX; // Maximum servo angle for extreme right turn (e.g., 120 degrees)
```

### Functions

#### `void driveForward(int speed)`

* **Purpose**: Engages the rear DC motors for forward propulsion.
* **Parameters**:
  * `speed`: An integer PWM value (0-255) that directly controls the motor's power and speed.
* **Operation**:
  * `analogWrite(MOTOR_INA_PWM, speed);`: Applies the specified PWM signal to control motor power.
  * `digitalWrite(MOTOR_INB_PWM, LOW);`: Sets the direction pin to `LOW` for forward movement.

#### `void driveBackward(int speed)`

* **Purpose**: Activates the rear DC motors to move the robot in reverse.
* **Parameters**:
  * `speed`: An integer PWM value (0-255) for backward motor power.
* **Operation**:
  * `analogWrite(MOTOR_INA_PWM, LOW);`: Sets the INA pin to `LOW`.
  * `digitalWrite(MOTOR_INB_PWM, speed);`: Applies the PWM signal to the INB pin, establishing the backward direction. This function is specifically utilized for controlled reverse maneuvers, such as during the parking sequence.

#### `void stopMotors()`

* **Purpose**: Deactivates the DC motors, allowing the robot to decelerate naturally.
* **Operation**:
  * `digitalWrite(MOTOR_INA_PWM, LOW);`
  * `digitalWrite(MOTOR_INB_PWM, LOW);`
        This method provides a gentle stop, reducing mechanical stress compared to an abrupt brake.

#### `void stopBrake()`

* **Purpose**: Implements an immediate and forceful braking action for the DC motors.
* **Operation**:
  * `digitalWrite(MOTOR_INA_PWM, HIGH);`
  * `digitalWrite(MOTOR_INB_PWM, HIGH);`
        By setting both motor input pins to `HIGH`, a short-circuit braking effect is achieved, resulting in a rapid stop. This is typically used for emergency halts or final system shutdown.

#### `void setSteeringAngle(int angle)`

* **Purpose**: Controls the angular position of the front steering wheels using the attached servo motor.
* **Parameters**:
  * `angle`: An integer representing the desired servo position in degrees (0-180).
* **Operation**:
  * `steeringServo.write(angle);`: Sends the `angle` command to the servo using the `Servo.h` library.
  * `angle = constrain(angle, SERVO_LEFT, SERVO_RIGHT);`: The `angle` value is constrained to remain within `SERVO_LEFT` and `SERVO_RIGHT` boundaries.
* **Safety**: It is important to constrain the angle into the maximum boundaries. This prevents over-rotation and physical interference with the chassis.

#### `void exitParking()`

* **Purpose**: Exits the parking zone by steering away from nearby walls based on real-time distance readings from ultrasonic sensors.
* **Operation**:
  1. **Distance Measurement**:
     ```cpp
     int distanceR = getDistance(sonarRight);
     int distanceL = getDistance(sonarLeft);
     ```
     The function begins by measuring the distance to the nearest  wall using the right and left ultrasonic sensors. These values are filtered by the `getDistance()` function to ensure stability and reduce noise.
     
  3. **Decision Logic Based on Proximity**:
     The robot determines which side is closer to a wall and selects an appropriate evasive maneuver:
     
     * **Wall on the Right**:

       ```cpp
       if (distanceR < 30 && distanceR != 0) {
           steeringServo.write(SERVO_STRAIGHT - 40);
           driveForward(220);
           safeDelay(1000);
       }
       ```
       If the right wall is within 30 cm and the reading is valid (not zero), the robot steers sharply to the **left** (by subtracting 40 from the straight angle) and drives forward at a moderate speed. The movement is sustained for 1000 milliseconds using a non-blocking `safeDelay()` to allow for orientation updates.

     * **Wall on the Left**:

       ```cpp
       else if (distanceL < 30 && distanceL != 0) {
           steeringServo.write(SERVO_STRAIGHT + 40);
           driveForward(220);
           safeDelay(1000);
       }
       ```
       
     Similarly, if the left wall is within 30 cm, the robot steers sharply to the **right** (adding 40 to the straight angle) and drives forward with the same parameters.

     * If neither wall is detected within the 30 cm threshold, the robot assumes it is centered and skips the exit parking maneuver entirely.

#### `void parkingManeuver()`

* **Purpose**: Executes a predefined parking maneuver, adapting to the robot's current turning `direction`.

* **Operation**:

    1. **Defining Math and Control Variables**

        ```cpp
        int distance = getDistance(sonarLeft); // The distance to the wall
        // Pythagorean theorem
        int a_cm = distance - 28; // a_cm is negative if the bot is too near to the wall
        int b_cm = 75; // Longitudinal distance
        int c_cm; // Diagonal distance
        int angle; // Angle of turn
        int turnDirection; // Used to know the direction of the turn; if a_cm is 0, this variable is 0 (no turn is required)
        ```
        Variables are changed according to the parking maneuver to be executed, which depends on the `direction`.

        The diagonal distance `c_cm` and the `angle` required to get near the parking lot is calculated using geometric concepts and trigonometry. 

    2. **Defining Turn Direction**

        ```cpp
        if  (a_cm > 0) { // Close to wall
          c_cm = sqrt(pow(a_cm, 2) + pow(b_cm, 2)); // Calculates the amount of pulses for diagonal movement
          turnDirection = 1;
        }
        else if (a_cm < 0){ // Far from wall
          c_cm = sqrt(pow(a_cm, 2) + pow(b_cm, 2)); // Calculates the amount of pulses for diagonal movement
          turnDirection = -1;
        } else { 
          c_cm = b_cm; // No amount of diagonal movement
          turnDirection = 0;
        }
        ```
        The `turnDirection` variable defines the orientation of the turn. If the robot is near the wall, it will proceed to turn outwards; conversely, if it's far from the parking, it will turn inwards. Moreover, there is a possibility `a_cm = 0`. For this case, no turn is required, indicating that `turnDirection` will be null.

    3. **Calculating Turn**

        ```cpp
        if (turnDirection != 0) { // Diagonal movement is required
          float tangent = ((float)abs(a_cm)/b_cm); // Calculate tangent
          angle = (int)(atan(tangent) * (180.0 / M_PI)); // Calculate required turn angle

          turnTargetYaw = (turnTargetYaw + (angle*direction*turnDirection)); // Adjustes target yaw
          setTargetYaw(turnTargetYaw); 
        } else { // No angle was required
          Serial.print(" - No angle required - ");
        }
        ```
        The required angle is calculated and applied to the target yaw.

    4. **Movement Execution**

        ```cpp
        encoderDelayOrientation(c_cm); // Waits until the defined distance is complete
        stopBrake();  // Stops the motors

        if (turnDirection != 0) { // Resets angles when distance is complete
          turnTargetYaw = (turnTargetYaw - (angle*direction*turnDirection));  // Resets the target yaw
          setTargetYaw(turnTargetYaw); // Applies the target yaw
        }
        ```

        The movement is executed, and the target yaw is reset, positioning the robot past the parking lot, aligned parallel to the outer wall.

    5. **Parking Sequence**: The robot moves backwards, the steering servo is turned to the direction of the parking, it reverses and steers to the opposite direction, calculating the amount of steps using `encoderDelay()`, completing the parking maneuver.

* **Adapted Parking Maneuver**: 

    1. **Block Detection**

        ```cpp
        bool parkingManeuverBlockDetection() {
          driveForward(parkingSpeed);
          encoderDelayOrientation(55); // advanced 5 cm.;

          stopBrake();
          delay(1000);
          readBlock(); // reads the blocks detected by the OpenMV camera

          if (!obstacleDetected()) {
            return false; // If no blocks detected, just false.
          }

          int blockSignature = currentColor;
          
          if (direction == +1 && blockSignature == SIGNATURE_RED) {
            return true;
          } else if (direction == -1 && blockSignature == SIGNATURE_GREEN) {
            return true;
          } else return false;
        }
        ```

        It first drives forward to detect and determine the few possible cases available: no block, red block or green block. After this detection, the robot will then proceed to execute the parking maneuver after reversing to its initial position. If the robot has to proceed to the outer wall to park, the same parking maneuver will be executed; however, if the robot has to proceed to the inner wall to evade an obstacle, the following steps are taken.

    2. **Obstacle Evasion**

        ```cpp
        int distance = getDistance(sonarLeft);
        int a_cm = (distance - 75);
        int b_cm = 75;
        int c_cm;
        int angle;
        int turnDirection;
        ```

        Triangle values are changed, as shown in the code block above. Turn direction is also changed, for the opposite direction must be taken in this maneuver. The same positioning algorithm is used.

        ```cpp
        driveForward(parkingSpeed);

        encoderDelayOrientation(39); // Waits until the defined distance is complete
        stopBrake();  // Stops the motors

        setSteeringAngle(SERVO_STRAIGHT); // Resets Servo Angle
        ```

        The robot now proceeds to drive foward to align itself parallelly to the walls.

    3. **Positioning Execution**

        ```cpp
        //Overwriting math variables
        distance = getDistance(sonarRight);
        a_cm = (distance - 57);
        b_cm = 75;
        c_cm;
        angle;
        turnDirection;
        ```

        The same positioning function is used, except the ultrasonic sensor used is swapped to the one located in opposite direction, since its closer to this wall, errors are less likely to happen.
      
    4. **Parking Maneuver Sequence**

        The robot now proceeds to execute the standard parking coreography, advancing to align itself, then driving backwards and steering to park itself in the designated area. For a graphic representation of this maneuver, please refer to [adapted parking maneuver](#adapted-parking-maneuver).

For a visual explanation of the robot's parking system's [parking maneuver](#parking-maneuver).
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

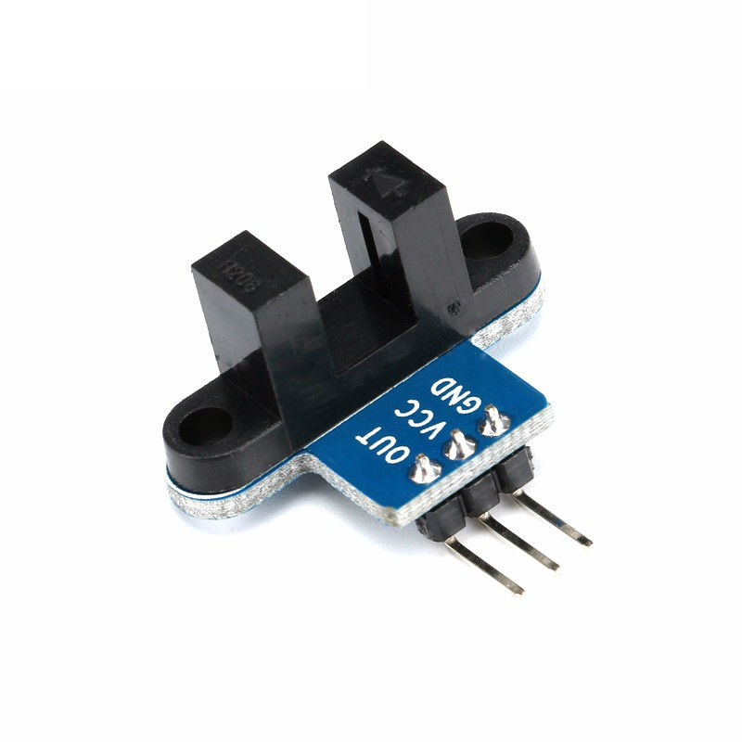
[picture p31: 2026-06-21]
assets/hardware_photos/encoder_pins.jpg

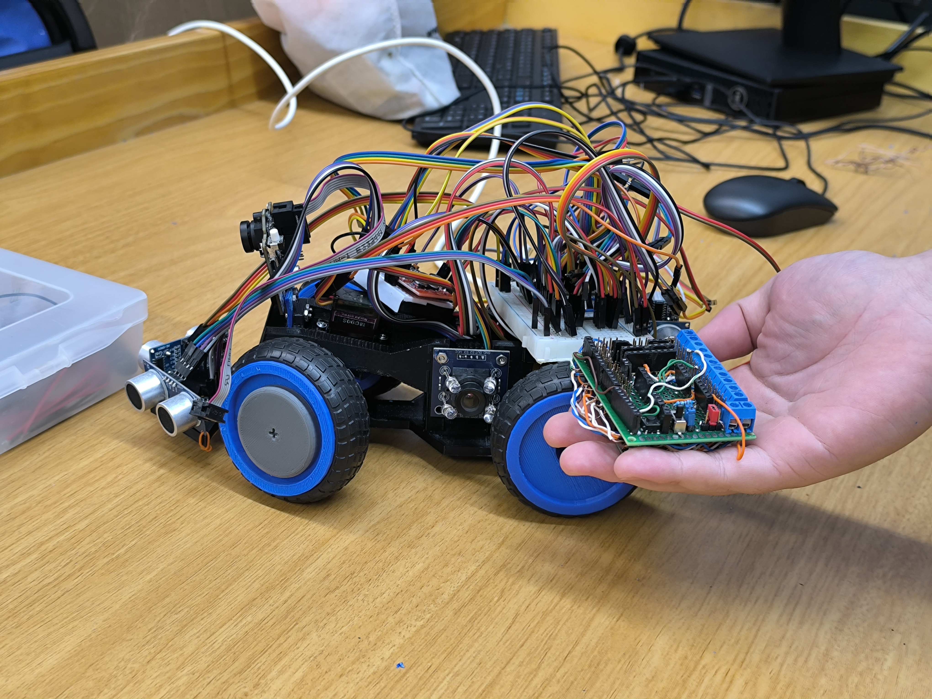
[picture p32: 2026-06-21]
assets/hardware_photos/imagen (6).jpg

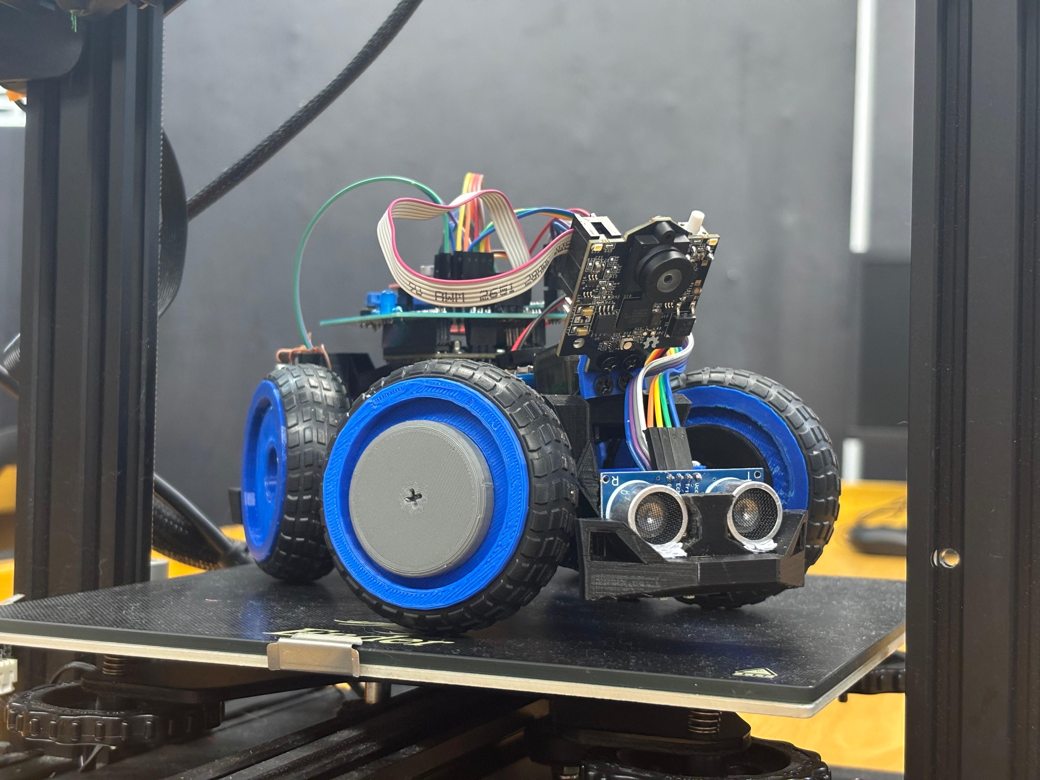
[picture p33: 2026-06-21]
assets/hardware_photos/ViZio_Photos/ViZioV3a.jpg

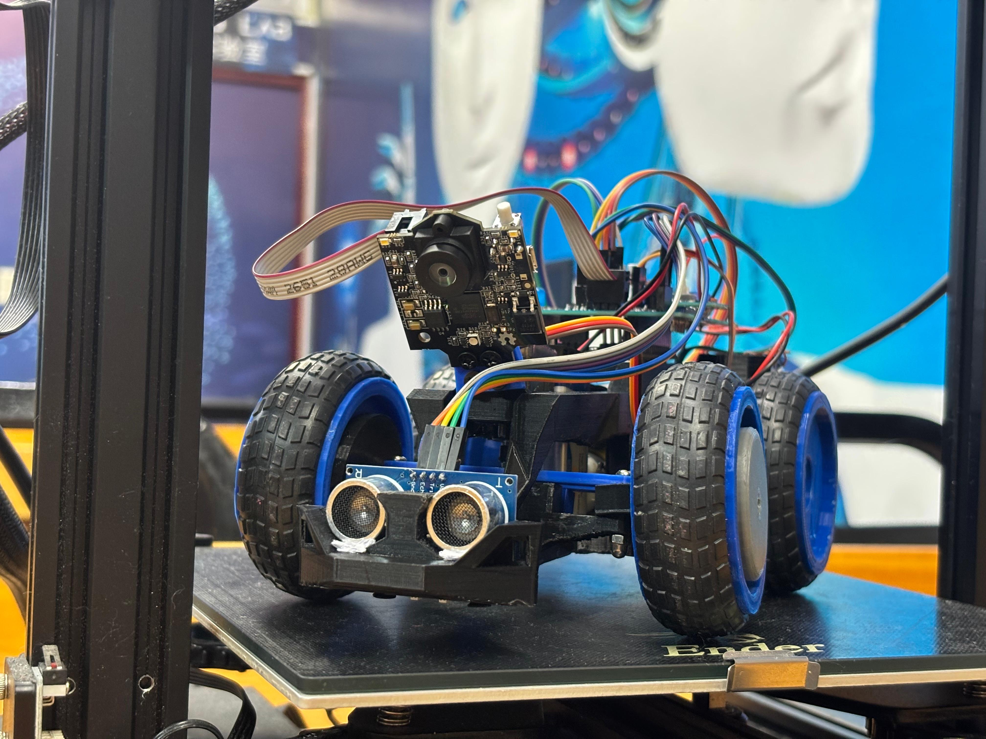
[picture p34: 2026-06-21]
assets/hardware_photos/ViZio_Photos/ViZioV3d.jpg

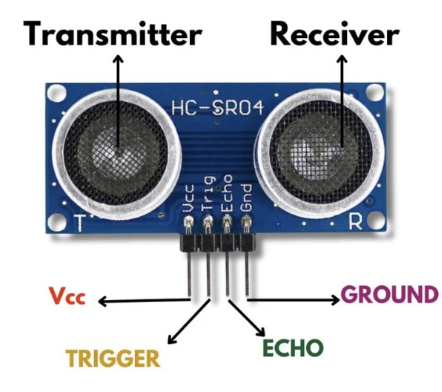
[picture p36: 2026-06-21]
assets/hardware_photos/Ultrasonic_pins.png

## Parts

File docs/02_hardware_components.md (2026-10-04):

# 2. Robot Hardware and Components

This section provides a detailed enumeration and description of all hardware components integrated into the robot and their specifications.

## 2.1 Main Control and Processing Unit

### **Component:**  **MEGA 2560 Pro Embed**

* **Quantity:** 1
* **Voltage:** 5V (operating), 7-9V (Vin)
* **Description:** Serves as the main controller board, based on the ATmega2560 microcontroller. It processes all sensor data, executes control algorithms, and manages actuation.
* **Features:** 54 digital I/O pins, 16 analog inputs, 256 KB flash memory, and 16 MHz clock speed.

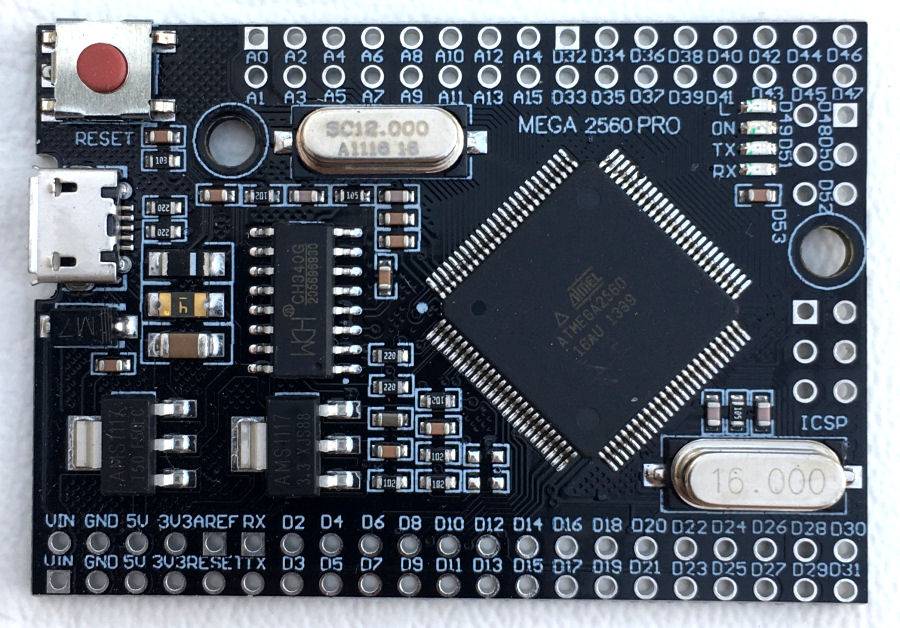
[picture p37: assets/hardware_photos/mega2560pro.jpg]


## 2.2 Motion System Components

### **Component:** **Hobby Gearmotor with 48:1 gearbox**

* **Quantity:** 1
* **Voltage Range:** 3-12V (operating at ~8V)
* **Current Consumption** ~120 mA
* **Stall Torque:** ~1.5 kg·cm (0.15 N·m)
* **Stall Current:** ~1.6 A
* **Description:** A brushed DC motor with an integrated gearbox for increased torque. Utilized for rear-wheel propulsion.

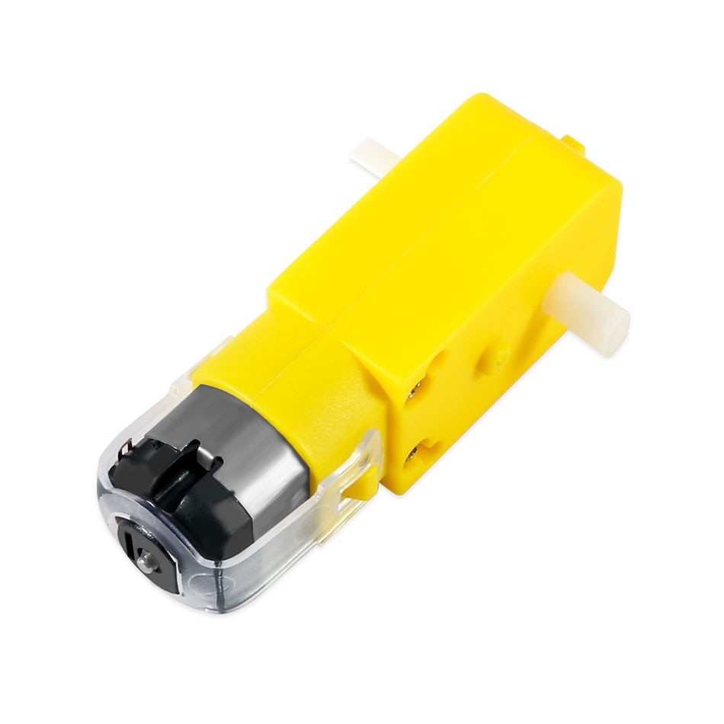
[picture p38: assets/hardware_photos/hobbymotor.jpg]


### **Component:** **Servo Motor MG90S**

* **Quantity:** 1
* **Voltage Range:** 4.8-6V
* **Current Consumption:** ~250 mA (max)
* **Torque:** 1.8 kg·cm @ 5V (0.18 N·m)
* **Description:** A micro servo motor employed for front-wheel steering. Operates via PWM signal.

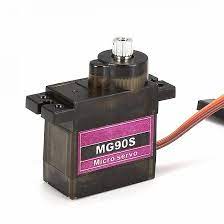
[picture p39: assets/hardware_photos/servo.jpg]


### **Component:** **Mini MX1508 Motor Driver**

* **Quantity:** 1
* **Logic Voltage:** 5V
* **Motor Voltage Range:** Up to 12V
* **Current Output:** Up to 2A per channel
* **Description:** A dual H-bridge motor driver responsible for interfacing the low-current control signals from the Arduino Mega to the higher-current requirements of the DC motors.

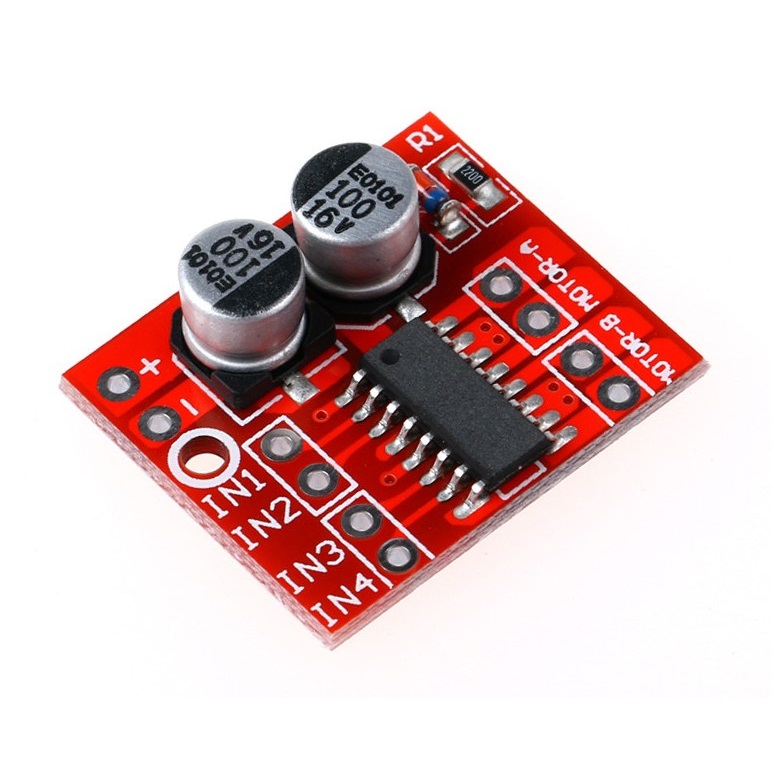
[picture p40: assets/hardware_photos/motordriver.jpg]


### **Mechanism**: **Mechanical Differential**

* **Quantity**: 1
* **Gear Ratio**: 1.8:1
* **Material**: Nylon and steel.
* **Description**: A gear assembly that splits engine torque evenly between two wheels while allowing them to rotate at different speeds.



## 2.3 Sensor Suite

### **Component:** **OpenMV H7 Plus**

* **Quantity:** 1
* **Voltage:** 3.6–5V (via VIN) / 3.3V logic (5V tolerant for most pins)
* **Current Consumption:** ~140 mA
* **Interface:** USB, UART, I²C, SPI
* **Description:** Embedded machine-vision camera module capable of real-time image processing using MicroPython. It includes an STM32H7 microcontroller and camera sensor, allowing tasks such as color tracking, object detection, line following, and AprilTag recognition. In this project it is used for obstacle detection and color-based navigation.

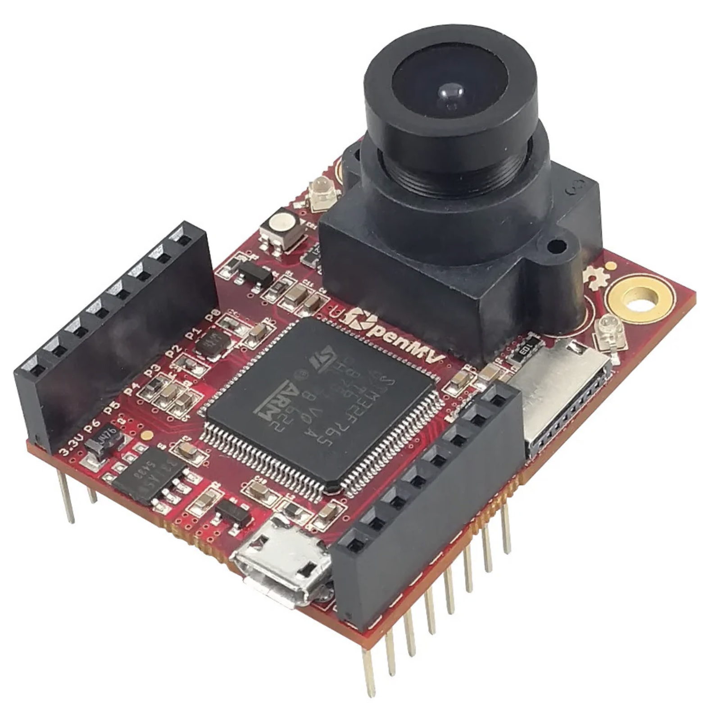
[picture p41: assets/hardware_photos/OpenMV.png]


### **Component:** **TCS3472 Color Sensor**

* **Quantity:** 1
* **Voltage:** 3.3-5V
* **Current Consumption** ~235 µA (active)
* **Interface:** I2C
* **Description:** High-resolution color sensor with IR filtering. Mounted underneath the robot to detect blue and orange floor lines that indicate turns.

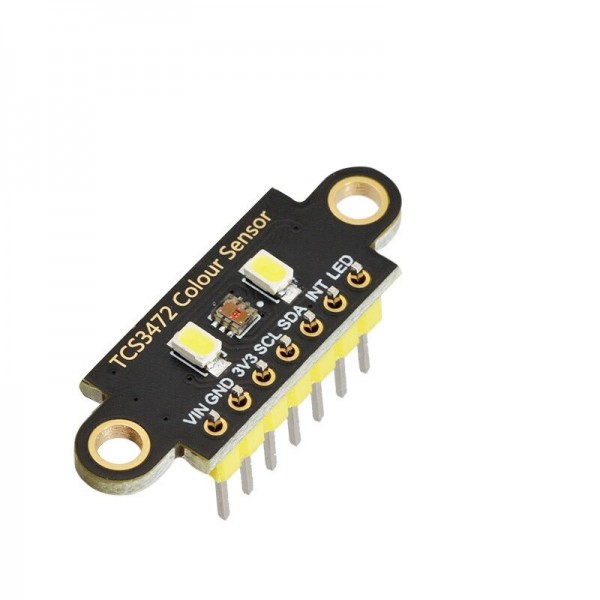
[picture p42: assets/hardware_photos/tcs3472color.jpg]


### **Component:** **HC-SR04 Ultrasonic Sensors**

* **Quantity:** 4
* **Voltage:** 5V
* **Current Consumption:** ~15 mA
* **Range of Detection:** ~2 cm to ~4 m
* **Description:** Distance sensors placed at the front and rear utilized for measuring real-time distances to walls, used for collision avoidance and maintaining orientation.

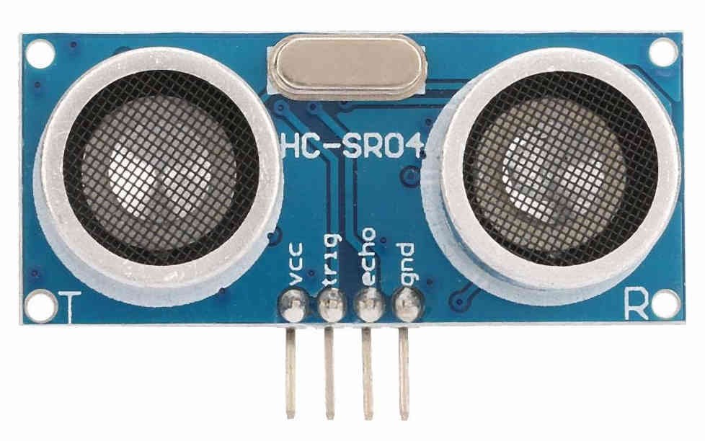
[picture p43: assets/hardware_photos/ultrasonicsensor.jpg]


### **Component:** **MPU6050 Accelerometer + Gyroscope**

* **Quantity:** 1
* **Voltage:** 3.3-5V
* **Current Consumption:** ~3.8 mA
* **Interface:** I2C
* **Description:** A 3-axis MPU providing acceleration and angular velocity data, used for angle correction and maintaining trajectory stability through PID control.

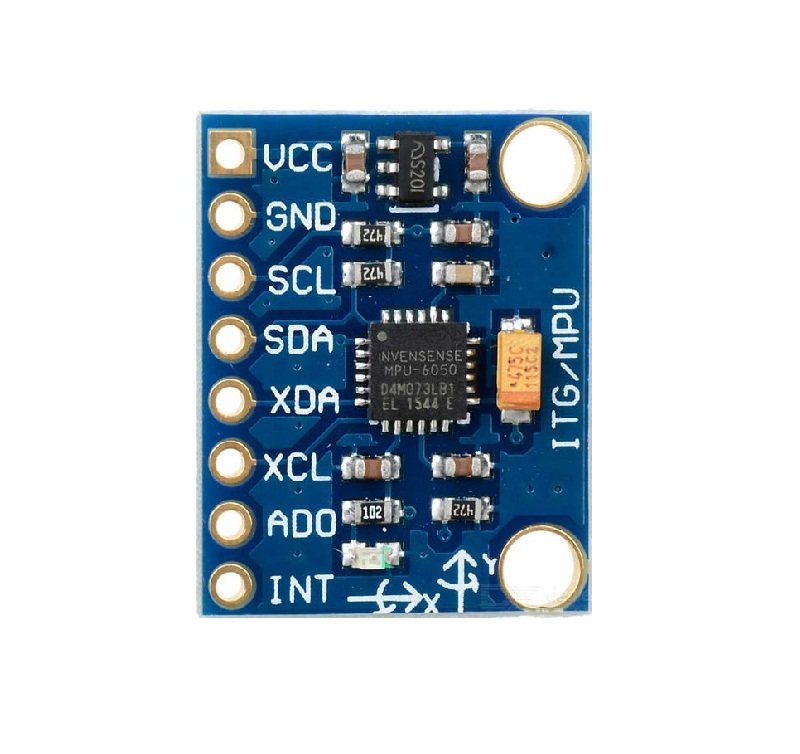
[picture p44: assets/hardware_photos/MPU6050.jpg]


### **Component:** **Infrared Optocoupler Encoder**

* **Quantity:** 1
* **Voltage:** 3.3-5V
* **Current Consumption:** <20 mA
* **Description:** A laser interruption-based encoder used for detecting rotational position, enabling accurate measurement of distance and speed (odometry).



## 2.4 Power Supply and Regulation

### **Component:** **4.2V batteries/3.7V**

* **Quantity:** 2
* **Voltage:** 4.2V fully charged, 3.7 nominal
* **Capacity:** 8800 mAh, 5000 mAh (~3000 mAh effective usable capacity)
* **Discharge Current:** Up to 2A (depending on model)
* **Description:** Power supply for the robot's DC motors and auxiliary LED headlights. Specifically, **Li-ion 18650 Battery 4.2V 8800 mAh** and **Li-ion 18650 Battery 3.7V 5000 mAh** are used alternatively.



### **Component:** **Rechargable 9V Battery**

* **Quantity:** 1
* **Voltage:** 9V nominal
* **Capacity:** ~600 mAh
* **Description:** A standard 9V battery used for the sensors and Arduino MEGA unit.



### **Component:** **Buck Converter**

* **Quantity:** 1
* **Voltage:** ~8V to 5V
* **Description:** A buck converter to step down voltage from the motor power supply (8.4V) to the servomotor (5V operation). 



## 2.5 Miscellaneous Components

  ### **Component:** **Custom Chassis (RWD)**

  * **Quantity:** 1
  * **Material:** 3D printed (PLA)
  * **Description:** A 3D designed rear-wheel drive chassis designed to house motors, mounts, sensors, battery holders, mechanical differential, and the controller.

  [**3D Modeling**](./10_3d_modeling.md)

  ### **Component:** **Pushbutton**

  * **Quantity:** 1
  * **Voltage Handling:** Signal-level (logic input)
  * **Current:** <10 mA
  * **Description:** A momentary switch used to initiate the main program.

  

  ### **Component:** **Self-Locking Push Button Switch**

  * **Quantity:** 1
  * **Voltage Handling:** Up to ~12V
  * **Current:** Up to ~500mA
  * **Description:** A switch for toggling between two states, serving as the main power switch for the robot.

 

  ### **Component:** **LED**

  * **Quantity:** 1
  * **Forward Voltage:** ~3V
  * **Current:** ~10-20 mA
  * **Description:** A standard blue LED used as a visual indicator, signaling program readiness.

  

  ### **Component:** **Headlight LEDs**

  * **Quantity:** 2
  * **Forward Voltage:** ~3V
  * **Current:** ~10-20 mA
  * **Description:** Standard white LEDs used as headlights for the bot.

  

  ### **Component:** **Resistor**

  * **Quantity:** 2
  * **Resistance:** 330Ω, 10kΩ
  * **Description:** Current-limiting resistor for the LED indicator 
  and pushbutton.
  
  

## 2.6 Removed Components

### **Component:** **TCS3200 Color Sensor (Removed in ViZio 2.0)**

* **Quantity:** 2
* **Voltage:** 2.7-5.5V
* **Power Consumption:** ~10-50 mA
* **Output:** Frequency proportional to color intensity
* **Description:** Side-mounted color recognition sensors used for detecting the magenta signal for parking. Converts color input to frequency output.



### **Component:** **PixyCam 2.1 (Replaced by the OpenMV in ViZio IV)**

* **Quantity:** 1
* **Voltage:** 5V
* **Current Consumption:** ~140 mA
* **Interface:** ICSP
* **Description:** Smart vision sensor for real-time color and object recognition. Used for obstacle detection. For information regarding removal, please refer to: [Component Selection](#27-component-selection).



## 2.7 Power Management  

The robot integrates a **dual-supply power architecture** to balance performance, efficiency, and protection of sensitive electronics:  

### Motor Power Supply  
* **Source:** **2x** [4.2V 18650 Li-ion Battery (~3000 mAh effective usable capacity)](#component-42v-batteries37v)  
* **Load:** [DC gearmotor](#component-hobby-gearmotor-with-481-gearbox), [L298N motor driver](#component-mini-l298n-motor-driver) + [Servo Motor](#component-servo-motor-mg90s) + [LED Headlights](#component-headlight-leds) (optional)  
* **Current Draw:**  
  * ~120 mA average during motion  
  * +40 mA with headlights (2 × 20 mA)  
  * Up to ~1.6 A at stall (short bursts only)
  * Servomotor ~70–160 mA average
* **Estimated Runtime:**  
  * Continuous average draw (~280 mA): ~70 hours  
  * With headlights (~320 mA): ~55 hours  
  * Realistic mixed load with peaks: **7-9 hours** of operation  

This battery is dedicated to propulsion and lighting, ensuring that motor noise and current surges do not affect sensor accuracy or logic circuits while maintaining long-lasting illumination for optimal operation.

### Logic and Sensor Power Supply

* **Source:** [Rechargeable 9 V Battery (~600 mAh)](#component-rechargable-9v-battery)
* **Load:** [MEGA 2560 Pro](#component--mega-2560-pro-embed) (voltage regulator) + [OpenMV](#component-openmv-h7-plus) + [MPU6050](#component-mpu6050-accelerometer--gyroscope) + [Color Sensor](#component-tcs3472-color-sensor) + [Ultrasonics](#component-hc-sr04-ultrasonic-sensors)  
* **Current Draw:**  
  * MEGA 2560 Pro: ~50–70 mA  
  * OpenMV H7: ~140 mA  
  * MPU6050: ~4 mA  
  * TCS3472 Color Sensor: ~0.24 mA  
  * Ultrasonic Sensors (x3): ~60 mA total  
  * **Total Average:** ~260–300 mA  
* **Estimated Runtime:**  
  * ~600 mAh / 280 mA ≈ **2 hours** continuous operation  
  * Recommended use time ≈ **1 hour** for best performance

This battery ensures clean and stable voltage delivery for sensors and the controller.  

### Voltage Regulation

* The **MEGA 2560 Pro** regulates the 9V input to 5V for its logic and peripherals.
* The **Buck Converter** steps down the motor power supply from 8.4V to 5V for safe servomotor operation, this module avoids current loss in heat, improving the system's efficiency.
* I²C devices (MPU6050, color sensors) operate safely at 3.3–5V.  

### Switching and Protection

* **[Main Switch](#component-self-locking-push-button-switch)**: Master power cutoff for the system.  
* **[Pushbutton](#component-pushbutton)**: Starts the main program after initialization.  
* **[330Ω and 10kΩ Resistor](#component-resistor)**: Ensures safe current limiting for the LED indicator and facilitates pushbutton grounding.
* **[LED Indicator](#component-led)**: Shows program readiness.  
* **[Headlight LEDs (x2)](#component-headlight-leds)**: White LEDs for illumination during operation.  

**Summary of Power Autonomy**  

* **Motors (4.2V Li-ion):** 7–9 hours
* **Logic & Sensors (9V battery):** ~2 hours (main limiting factor)  

The system's autonomy is therefore governed by the 9V supply, after which recharging or replacement is required.

## 2.8 Circuit Design

The robot utilizes a custom-made PCB, avoiding unnecessary clutter and improving overall order.



You can also download the fixed circuit files: [kicad_pcb](../src/kicad_pcb).

---

[Back to Main README.md Index](../README.md)

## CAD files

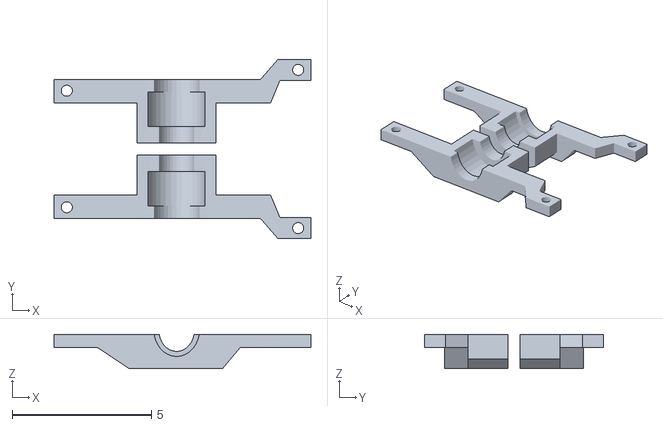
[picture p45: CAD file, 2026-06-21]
models/chassis/Lig2.stl
9.24 x 6.44 x 1.24

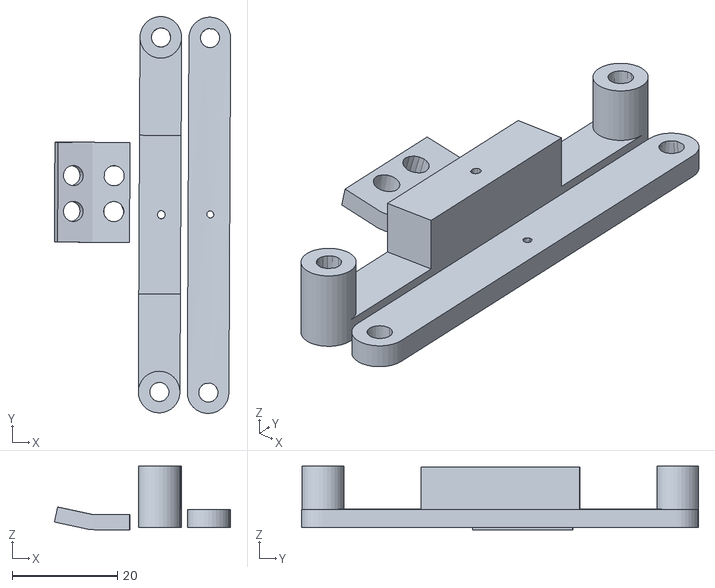
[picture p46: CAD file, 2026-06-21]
models/steering/steering_rods.stl
33.4 x 75.3 x 12.0

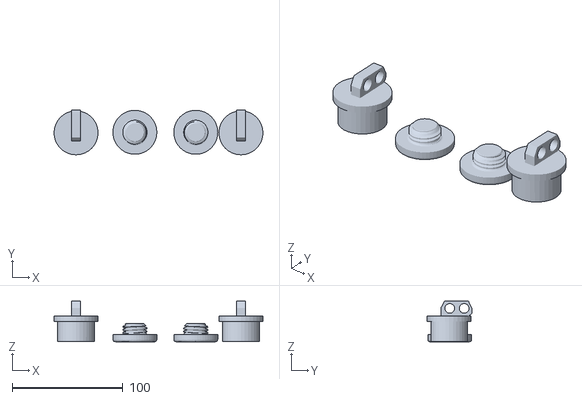
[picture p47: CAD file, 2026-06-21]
models/wheels/wheel_hub.stl
188.9 x 40.4 x 36.7

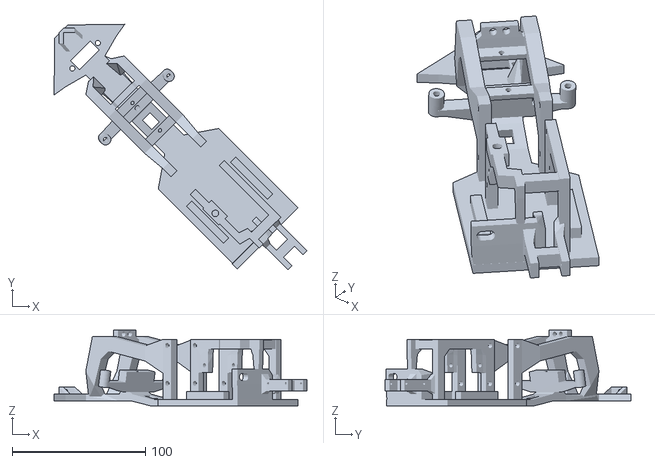
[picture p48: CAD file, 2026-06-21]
models/chassis/chassis.stl
189.9 x 184.2 x 56.9

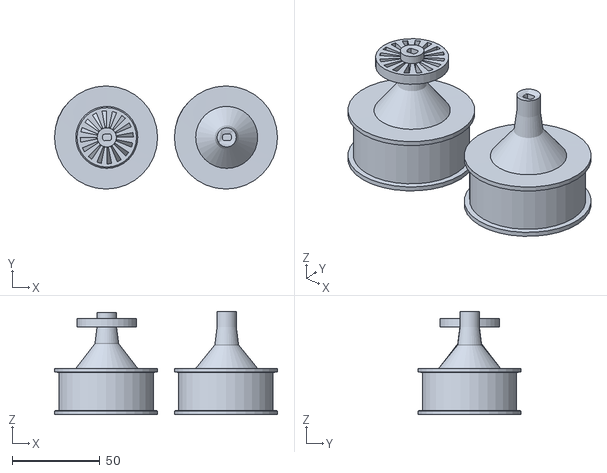
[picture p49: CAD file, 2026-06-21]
models/wheels/encoder_wheel.stl
127.3 x 58.9 x 58.8

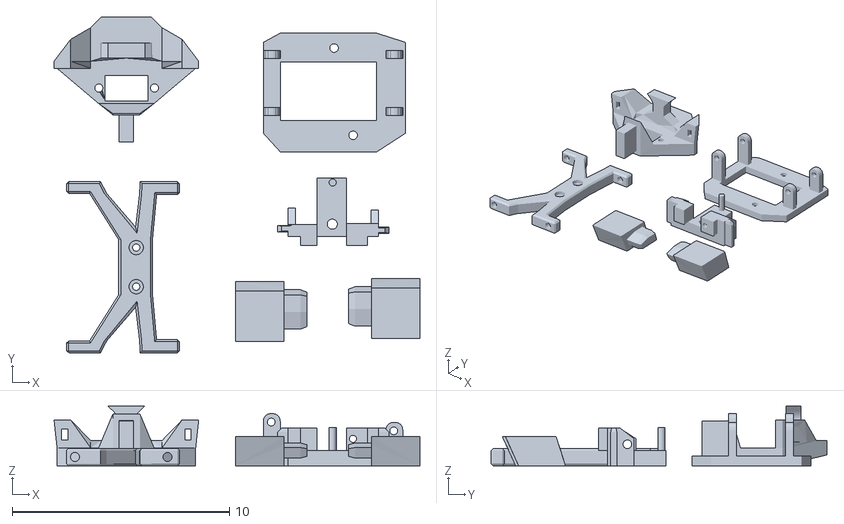
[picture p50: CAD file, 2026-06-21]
models/chassis/ViZio26CalcModel_VXMisc.stl
16.8 x 15.4 x 2.76

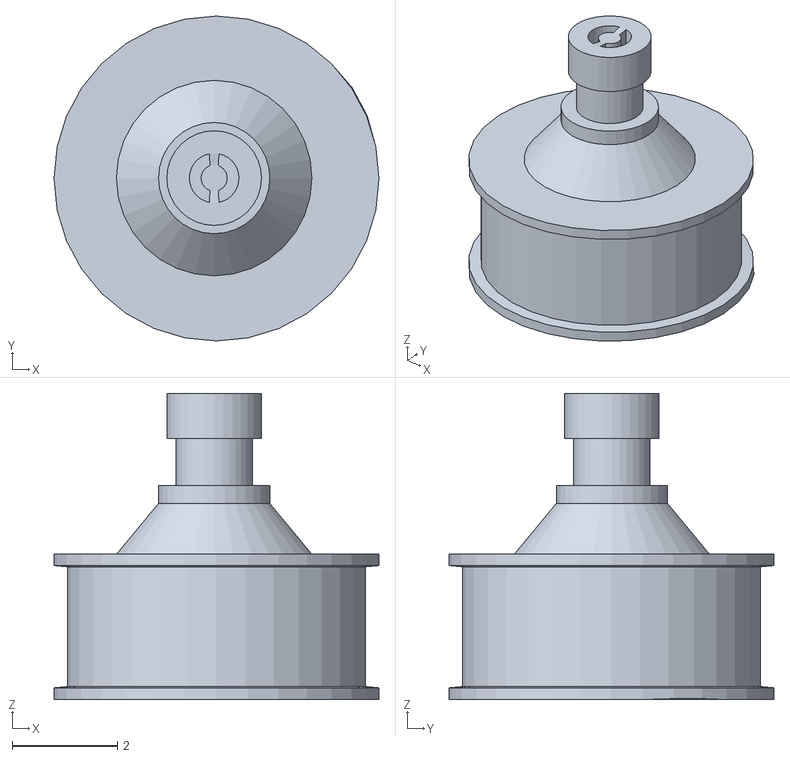
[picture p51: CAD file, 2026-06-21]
models/wheels/ViZio26CalcModel_WheeL.stl
6.19 x 6.18 x 5.83

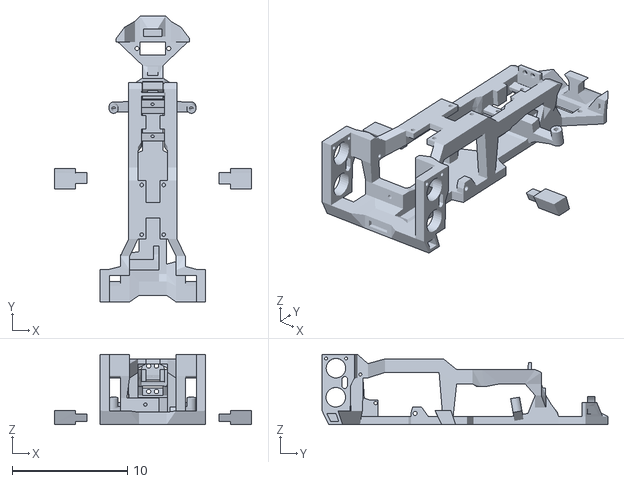
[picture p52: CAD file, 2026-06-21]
models/chassis/chassis2.0.stl
17.1 x 24.8 x 6.10

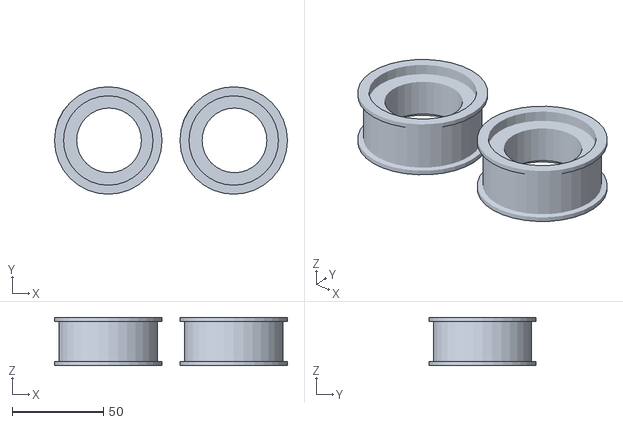
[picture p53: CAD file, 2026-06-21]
models/wheels/wheel_rims.stl
127.5 x 58.8 x 26.4

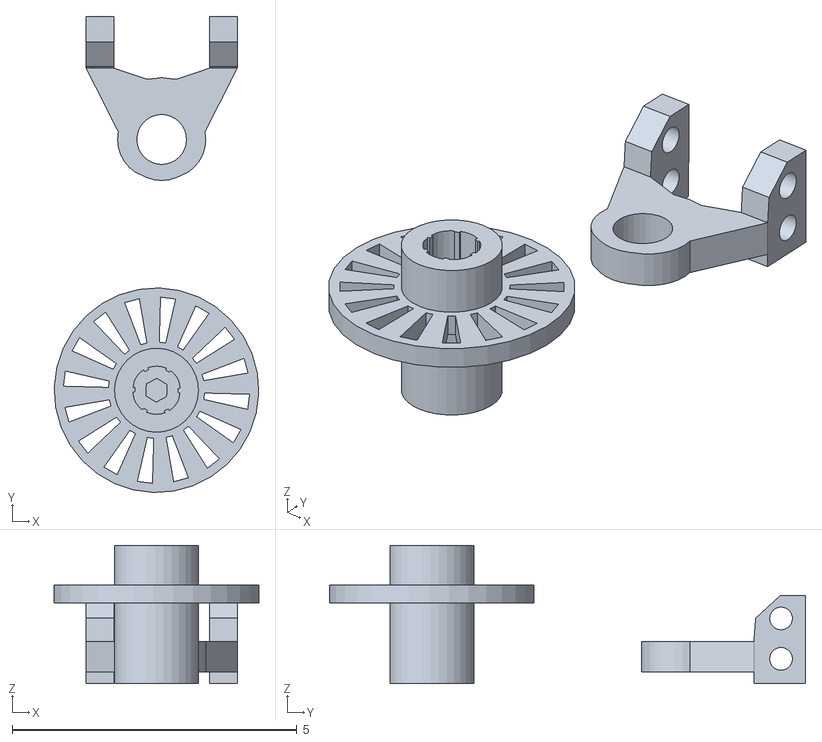
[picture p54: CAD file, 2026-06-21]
models/chassis/AxleAndSupport.stl
3.59 x 8.36 x 2.43

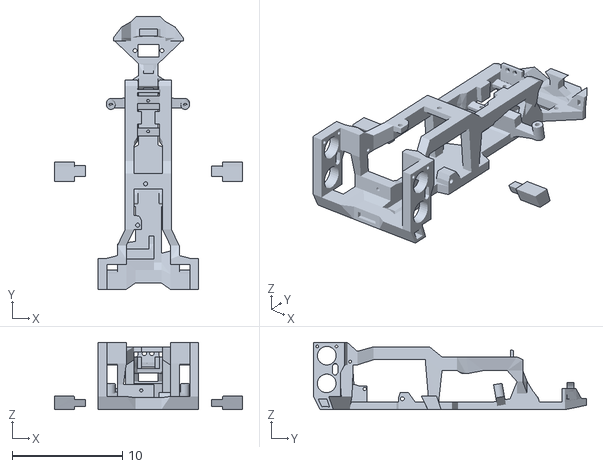
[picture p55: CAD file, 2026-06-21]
models/chassis/ViZioInternationalMotorFix.stl
17.1 x 24.8 x 6.10

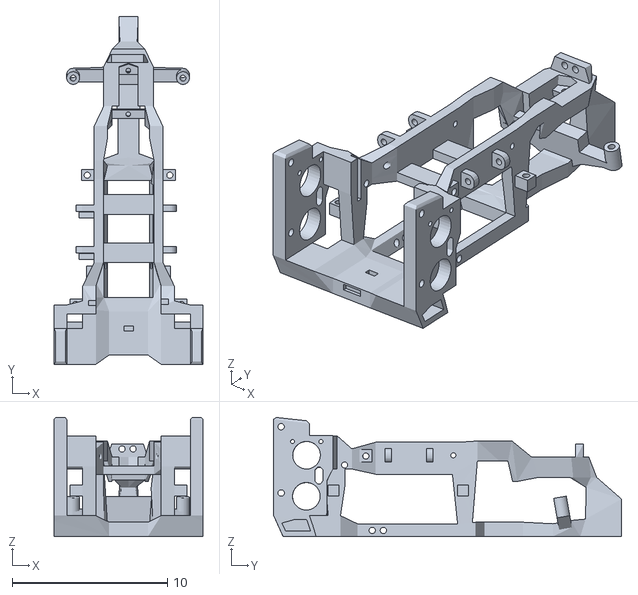
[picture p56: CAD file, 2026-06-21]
models/chassis/ViZio26V4Chassis.stl
9.59 x 22.4 x 7.66

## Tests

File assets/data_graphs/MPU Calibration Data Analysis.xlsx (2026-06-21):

samples | accumulated error
10 | 0.105206
25 | 0.132352
50 | 0.065165
100 | 0.032352
150 | 0.014112
200 | 0.004077
300 | 0.003492
500 | 0.002473
750 | 0.001029
1000 | 0.001671

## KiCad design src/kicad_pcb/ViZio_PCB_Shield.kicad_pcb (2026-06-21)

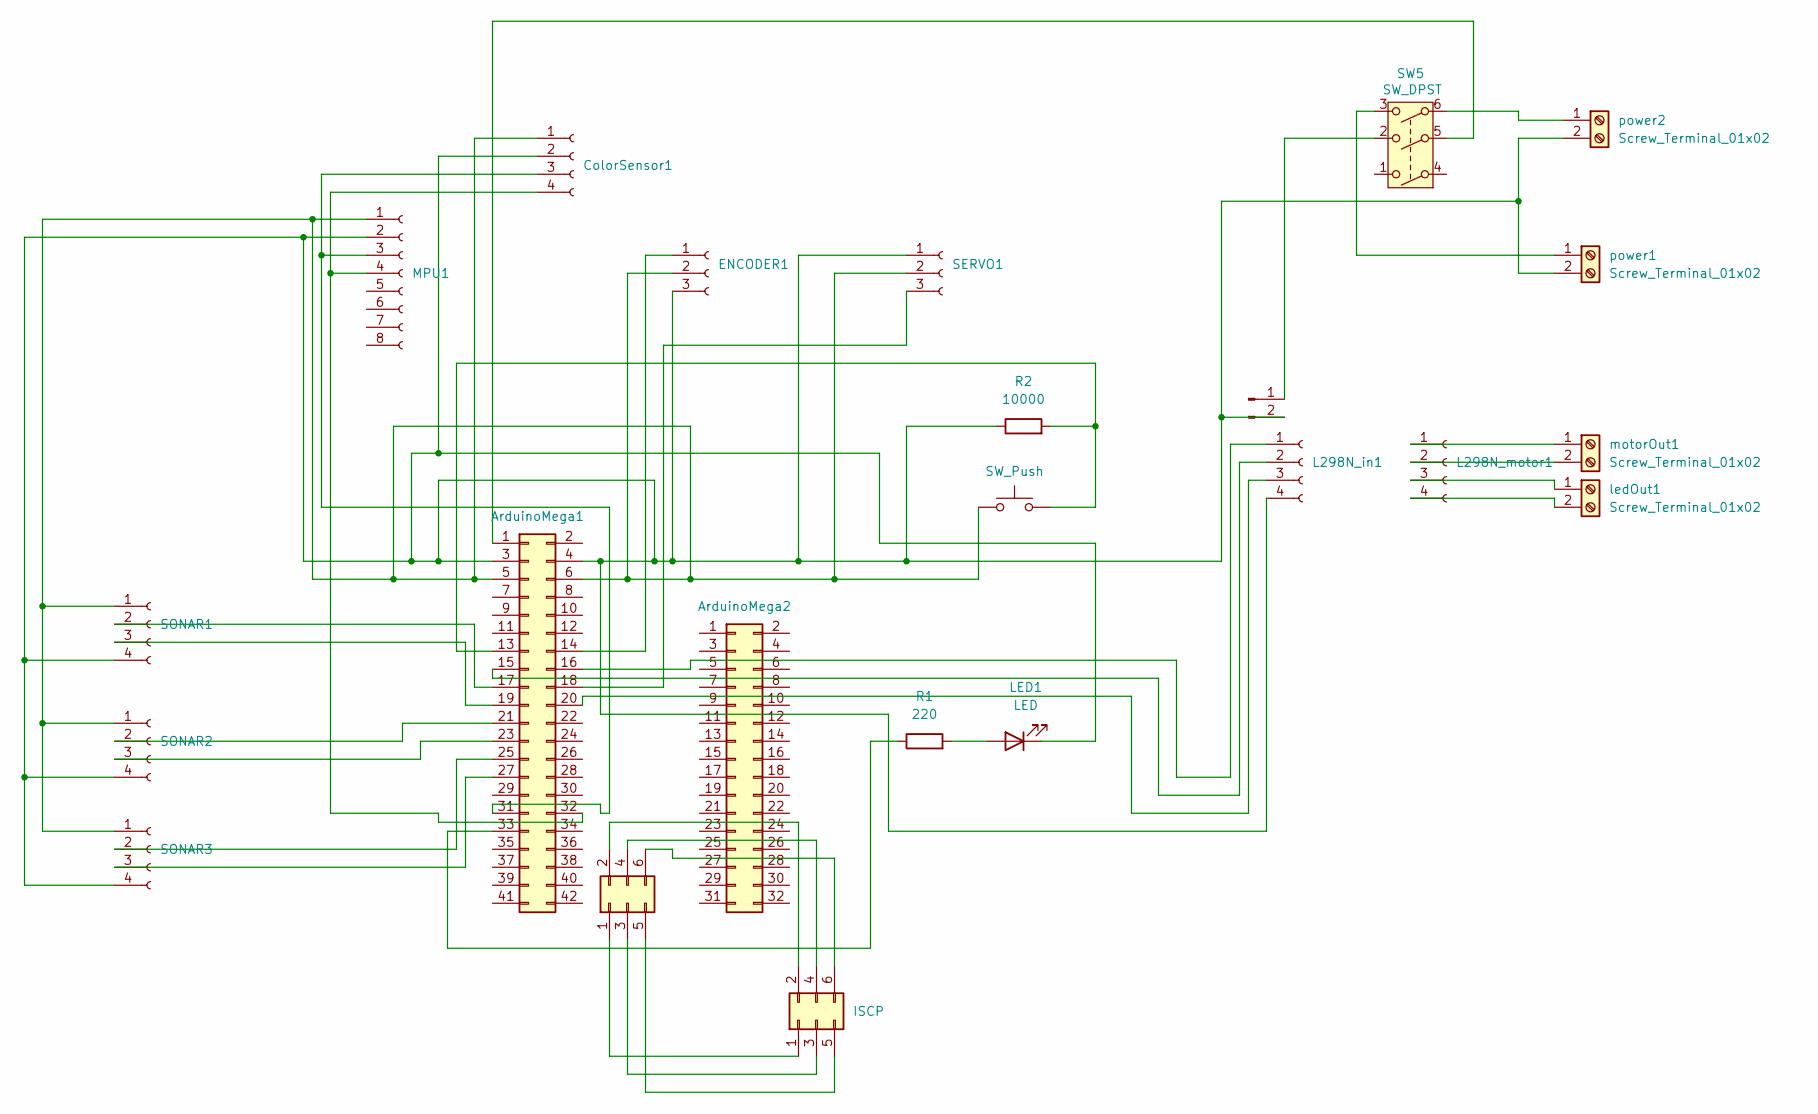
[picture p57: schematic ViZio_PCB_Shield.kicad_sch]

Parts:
ColorSensor1: Conn_01x04_Socket; PinSocket_1x04_P2.54mm_Vertical
ENCODER1: Conn_01x03_Socket; PinSocket_1x03_P2.54mm_Vertical
J1: ArduinoMega1; PinSocket_2x21_P2.54mm_Vertical
J2: ISCP; PinHeader_2x03_P2.54mm_Vertical
J3: ArduinoMega2; PinSocket_2x16_P2.54mm_Vertical
J4: Conn_02x03_Odd_Even; PinSocket_2x03_P2.54mm_Vertical
L298N_in1, L298N_motor1: Conn_01x04_Socket; PinSocket_1x04_P2.54mm_Vertical
L298N_power1: Conn_01x02_Pin; PinSocket_1x02_P2.54mm_Vertical
LED1: LED; LED_D5.0mm
MPU1: Conn_01x08_Socket; PinSocket_1x08_P2.54mm_Vertical
R1: 220; R_Axial_DIN0207_L6.3mm_D2.5mm_P10.16mm_Horizontal
R2: 10000; R_Axial_DIN0207_L6.3mm_D2.5mm_P10.16mm_Horizontal
SERVO1: Conn_01x03_Socket; PinHeader_1x03_P2.54mm_Vertical
SONAR1, SONAR2, SONAR3: Conn_01x04_Socket; PinSocket_1x04_P2.54mm_Vertical
SW1: SW_Push; SW_PUSH_6mm_H5mm
SW5: SW_DPST; SW_Push_2P2T_Toggle_CK_PVA2OAH5xxxxxxV2
ledOut1: Screw_Terminal_01x02; TerminalBlock_bornier-2_P5.08mm
motorOut1: Screw_Terminal_01x02; TerminalBlock_bornier-2_P5.08mm
power1, power2: Screw_Terminal_01x02; TerminalBlock_bornier-2_P5.08mm

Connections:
unnamed: ColorSensor1.2 (GND), ENCODER1.3 (GND), J1.3 (GND), J1.4 (GND), L298N_in1.4 (IN4), L298N_power1.2 (-), LED1.1 (K), MPU1.2 (GND), R2.1, SERVO1.1 (GND), SONAR1.4 (GND), SONAR2.4 (GND), SONAR3.4 (GND), power1.2 (-), power2.2 (-)
unnamed: ColorSensor1.3 (SCL), J1.31 (D21), MPU1.3 (SCL)
unnamed: ColorSensor1.4 (SDA), J1.32 (D20), MPU1.4 (SDA)
unnamed: ColorSensor1.1 (VCC), ENCODER1.2 (VCC), J1.5 (5V), J1.6 (5V), MPU1.1 (VCC), SERVO1.2 (VCC), SONAR1.1 (VCC), SONAR2.1 (VCC), SONAR3.1 (VCC), SW1.1
unnamed: ENCODER1.1 (OUT), J1.14 (D2)
unnamed: J1.13 (D3), R2.2, SW1.2
unnamed: J1.16 (D4), L298N_in1.1 (IN1)
unnamed: J1.15 (D5), L298N_in1.2 (IN2)
unnamed: J1.18 (D6), SERVO1.3
unnamed: J1.17 (D7), SONAR1.2 (TRIG)
unnamed: J1.20 (D8), L298N_in1.3 (IN3)
unnamed: J1.19 (D9), SONAR1.3 (ECHO)
unnamed: J1.21 (D11), SONAR2.2 (TRIG)
unnamed: J1.23 (D13), SONAR2.3 (ECHO)
unnamed: J1.25 (D15), SONAR3.2 (TRIG)
unnamed: J1.27 (D17), SONAR3.3 (ECHO)
unnamed: J1.33 (D23), R1.1
unnamed: J1.1 (VIN), SW5.5
unnamed: J2.1, J4.1
unnamed: J2.2, J4.2
unnamed: J2.3, J4.3
unnamed: J2.4, J4.4
unnamed: J2.5, J4.5
unnamed: J2.6, J4.6
unnamed: L298N_motor1.2 (MOTOR_A2), motorOut1.2 (-)
unnamed: L298N_motor1.1 (MOTOR_A), motorOut1.1 (+)
unnamed: L298N_motor1.4 (MOTOR_B2), ledOut1.2 (-)
unnamed: L298N_motor1.3 (MOTOR_B), ledOut1.1 (+)
unnamed: L298N_power1.1 (+), SW5.2
unnamed: LED1.2 (A), R1.2
unnamed: SW5.3, power1.1 (+)
unnamed: SW5.6, power2.1 (+)

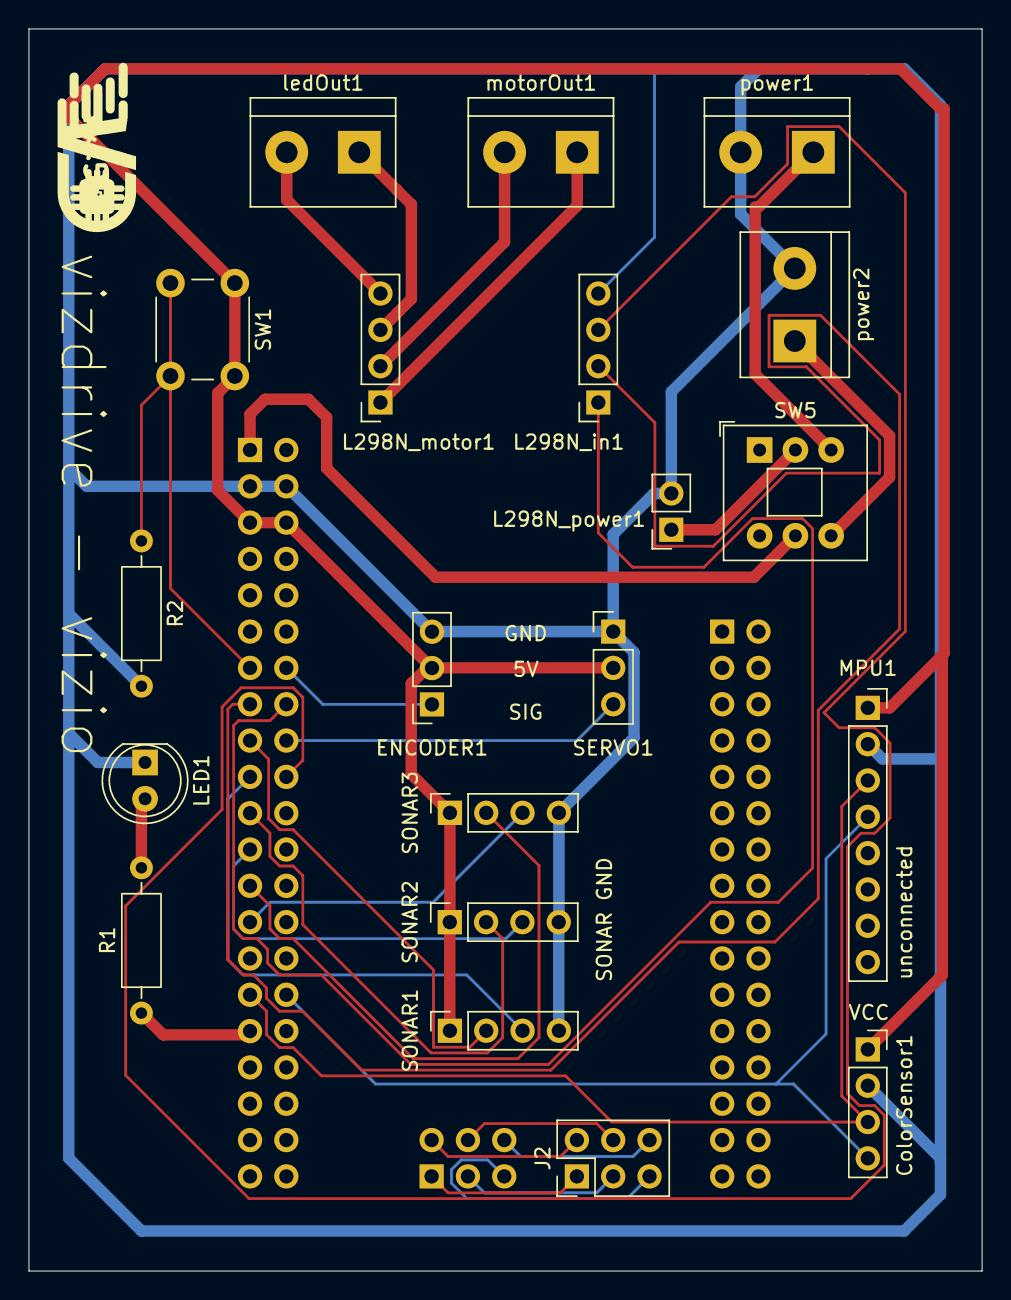
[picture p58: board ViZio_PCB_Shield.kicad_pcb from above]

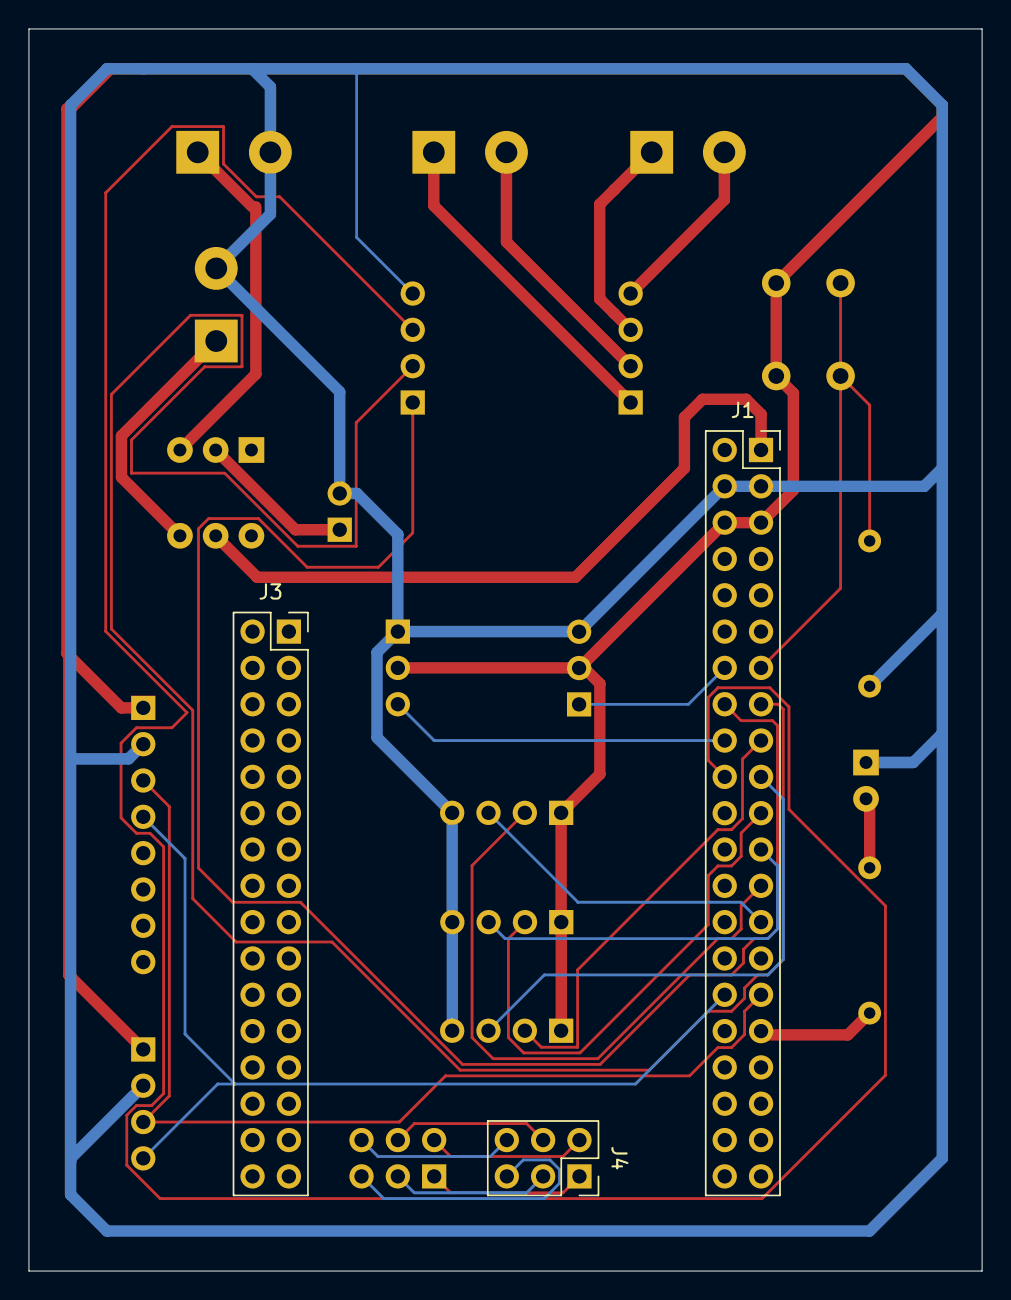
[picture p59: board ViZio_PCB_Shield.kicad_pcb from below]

Board: 2 copper layers, 66.7 x 86.9 mm, 23 parts (3 on the bottom side), 32 nets.

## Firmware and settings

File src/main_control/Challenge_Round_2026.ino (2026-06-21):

#include <Wire.h> // I2C connection
#include <Adafruit_MPU6050.h> // MPU-6050
#include <Adafruit_Sensor.h>
#include <Adafruit_TCS34725.h>  // Color sensor
#include <Servo.h>  // Servo motor
#include <NewPing.h>  // Ultrasonic sensors
 
// GLOBAL VARIABLES
 
// 1. Mobility Functionalities
 
// DC motor PWM pins
#define MOTOR_INA_PWM 5
#define MOTOR_INB_PWM 4
float speedBoost = 1.1;
int motorSpeed = int(175 * (speedBoost)); //175
int parkingSpeed = int(155 * (speedBoost)); //155
int parkingReverseSpeed = int(155 * (speedBoost)); //155
int backwardSpeed = int(200 * (speedBoost)); //200

// Headlight PWM pins
#define LED_HEADLIGHT_PWM 8

// Servomotor pin
#define SERVO_PIN 6
 
// Constant servo angles
const int SERVO_STRAIGHT = 92;
int SERVO_MAX = 45; // maximum angle of servo's rotation
int SERVO_LEFT  = SERVO_STRAIGHT - SERVO_MAX;
int SERVO_RIGHT = SERVO_STRAIGHT + SERVO_MAX;

// Defining the servomotor
Servo steeringServo;

int turnAngle = 90; // Defining a variable to compensate for any constant offset in every turn
bool correctionApplied = false;  // Indicates if a correction was applied
float correctionAmount = 0.0;    // Stores what was the correction (±10.0)
 
// IR encoder pin
#define ENCODER_PIN   2
volatile unsigned long encoderPulseCount = 0; // volatile variable for pulse count
 
const float WHEEL_PERIMETER = 22.0; // cm
const float PULSES_PER_REVOLUTION = 16.0; // PPR
const float PULSES_PER_CM = PULSES_PER_REVOLUTION/WHEEL_PERIMETER;  // Pulses per cm
 
// 2. PID Control and Orientation

// Defining the MPU6050 with Adafruit library
Adafruit_MPU6050 mpu;
float gyroZ_offset = 0.0; // MPU6050 calibrated offset
 
static float yaw = 0.0; // variable for accumulated yaw
static float targetYaw = 0.0; // target yaw for PID correction
const int samples = 250;  // samples for MPU6050 calibration
int sensorFailCount = 0;
const int maxSensorFails = 10;  // Número máximo de fallos antes de actuar
 
static float previousError = 0.0; // previous error for the time derivative correction
 
// PID constants
const float Kp = 2.3; // proportional gain
const float Kd = 1.7; // derivative gain
const float Ki = 0.0; // integral gain (inactive to avoid wind-up and over-correction)
 
// 3. Color Detection
 
// color sensor located at the bottom
/*
const int BLUE_RED_THRESHOLD =   80;   // blue color thresholds. og = 80
const int BLUE_GREEN_THRESHOLD = 86;
const int BLUE_BLUE_THRESHOLD =  80;
const int ORANGE_RED_THRESHOLD =   110; // orange color thresholds
const int ORANGE_GREEN_THRESHOLD = 85;
const int ORANGE_BLUE_THRESHOLD =  70;
*/
// color sensor located at the bottom
const int BLUE_RED_THRESHOLD =   80;   // blue color thresholds. og = 80
const int BLUE_GREEN_THRESHOLD = 86;
const int BLUE_BLUE_THRESHOLD =  73;
const int ORANGE_RED_THRESHOLD =   112; // orange color thresholds
const int ORANGE_GREEN_THRESHOLD = 85;
const int ORANGE_BLUE_THRESHOLD =  60;

// Defining the i2c color sensor as "floorTcs"
static Adafruit_TCS34725 floorTcs(TCS34725_INTEGRATIONTIME_2_4MS, TCS34725_GAIN_1X);
 
// 4. Ultrasonic Sensor Distance Measurement
 
// Left ultrasonic sensor trigger and echo pins
#define US_LEFT_TRIG 15
#define US_LEFT_ECHO 17
// Right ultrasonic sensor trigger and echo pins
#define US_RIGHT_TRIG 11
#define US_RIGHT_ECHO 13

// Front ultrasonic sensor trigger and echo pins
#define US_FRONT_TRIG 7
#define US_FRONT_ECHO 9
 
// Max detection distance for the definition of the ultrasonic sensors
#define MAX_DISTANCE 200

// Defining the ultrasonic sensors with NewPing library
NewPing sonarFront(US_FRONT_TRIG, US_FRONT_ECHO, MAX_DISTANCE);
NewPing sonarLeft(US_LEFT_TRIG, US_LEFT_ECHO, MAX_DISTANCE);
NewPing sonarRight(US_RIGHT_TRIG, US_RIGHT_ECHO, MAX_DISTANCE);



// Signatures for the OpenMV color recognition
#define SIGNATURE_RED 2 //2
#define SIGNATURE_GREEN 1 //1
 
/*Configuration of the Region of Interest
Coordinates of the OpenMV's resolution: width: 160, height: 120*/
 
// Y-coordinate threshold for an object to be considered "near" and start evasion.
// Any part of the object below this Y-coordinate will trigger detection.
const int ROI_Y_BOUND = 119/6;
 
const int IMAGE_WIDTH = 159;
// Define sections of the image for evasion completion check
const int LEFT_SECTION_END_X = IMAGE_WIDTH / 4;   // X-coordinate separating left third
const int RIGHT_SECTION_START_X = (3 * IMAGE_WIDTH) / 4; // X-coordinate separating right third
 
// 6. State Logic

unsigned int lapTurnCount = 0;
int lapFinishedNumber = 12; // variables for lap counting
bool parkingMode = false, SystemShutdown = false; // variables for parking and shutdown

bool turningInProgress = false; // boolean that indicates when a turn was completed
unsigned long lastTurnTime = 0; // variable to control the turn cooldown
const float TURN_THRESHOLD = 3.0; // tolerance threshold for turns
unsigned long turnCorrectionTime = 3000000; // 4 seconds

bool correctionState = false;  // variable to avoid repetitive ultrasonic corrections in one lap

float turnTargetYaw = 0.0;  // target yaw for turning
int direction = 0;  // turn direction → -1: counterclockwise, +1: clockwise
 
int lastSignature = 0;  // last evaded signature for ultrasonic correction
int parkingSignature = 0;

// Miscellaneous
const int buttonPin = 3; // start button pin
const int ledPin = 23; // indicator LED
unsigned long lastUpdateOrientationTime = 0; // for main loop non-blocking delay
unsigned long lastUpdateTime = 0;
unsigned long lastCentreUpdateTime = 0; // for centring non-blocking while loop
 
void setup() {
  Serial.begin(115200); // initializing the serial monitor
  
  // Call all setup functions
  initMovement();
  initOrientation();
  initColorSensors();
  initUltrasonic();
  initVision();
  //initHeadlights(true, 150);
  initStateLogic();
 
  waitForStartButton(); // wait for button press
  lastUpdateTime = millis();
  exitParking();
}
 
void loop() {
  unsigned long now = millis(); // updates current time
 
  // Code executed at roughly 33.3 Hz
  if (now - lastUpdateTime < 25) return;  // if 30 ms have not passed, do not execute code
 
  //debugging();
 
  driveForward(motorSpeed); // drive forward with a specific speed
 
  updateOrientation();  // PID control and MPU6050 orientation control
  keepOrientation();  
 
  if (lapTurnCount > 0) recentreIfNeeded();  // avoid walls with ultrasonic sensors
 
  if (detectFloorColor()) handleColorAction();  // detect color lines on the floor for turns
  if (turningInProgress) completedTurn(); // function to detect completed turns

  if (obstacleDetected()) handleEvasion();  // detect obstacles and evade accordingly
  
  if (parkingMode == true) parkingManeuver(); // park after 3 laps

  lastUpdateTime = now; // updates the time for next iteration
}
 
// Functions
 
// Function for a non-blocking delay
// Only executes the updateOrientation function
void safeDelay(unsigned long ms) {
  unsigned long startDelay = micros();  // sets the start time
  unsigned long lastUpdateTimeD = 0UL; // para controlar la frecuencia de updateOrientation

  while ((micros() - startDelay) < ms*1000UL) {
    unsigned long nowD = micros(); // updates current time
    if (nowD - lastUpdateTimeD > 25000UL) {
      updateOrientation();  // updates orientation
      Serial.print("Remaining time: "); // debugging
      Serial.print((micros() - startDelay));
      Serial.println(" µs");
      lastUpdateTimeD = nowD; // updates the time for next iteration
    }
  }
  Serial.print("Finnished Delay----------------------------");
}

// Function for a non-blockaing delay
bool safeDelayColor(unsigned long ms) {
  unsigned long startDelay = micros();  // tiempo de inicio
  unsigned long lastUpdateTimeDC = 0UL; // para controlar la frecuencia de updateOrientation

  while ((micros() - startDelay) < ms * 1000UL) {
    unsigned long nowDC = micros();

    // Solo actualiza orientación cada 25 ms (25000 µs)
    if (nowDC - lastUpdateTimeDC >= 25000UL) {
      updateOrientation();
      lastUpdateTimeDC = nowDC;
    }

    if (detectFloorColor()) {
      handleColorAction();
      return true;  
    }

    delay(3);

    Serial.print("Remaining time: ");
    Serial.print(nowDC - startDelay);
    Serial.println(" µs");
  }

  Serial.println("Finished Delay-------------------- COLOR");
  return false; // si no hubo color, devuelve false
}

// SETUP FUNCTIONS
 
// Setup for Mobility Functionalities
void initMovement() {
  // DC Motor PWM pins as OUTPUT
  pinMode(MOTOR_INA_PWM, OUTPUT);
  pinMode(MOTOR_INB_PWM, OUTPUT);
  // Attach pin to the servo
  steeringServo.attach(SERVO_PIN);
  setSteeringAngle(SERVO_STRAIGHT); // set steering angle to straight in the setup
  pinMode(ENCODER_PIN, INPUT_PULLUP);
  attachInterrupt(digitalPinToInterrupt(ENCODER_PIN), encoderISR, RISING); // attach the interruption to the ISR, that counts the pulses
  Serial.println("Movement initialized...");
}
 
// Setup for Orientation Functionalities
void initOrientation() {
  Wire.begin(); // i2c connection to the MPU
  Wire.setWireTimeout(3000, true); // 3 ms timeout, reset bus on timeout
  while (!mpu.begin()) {
   Serial.println("MPU6050 not found, trying again in 3 seconds...");
   delay(3000);
  }
  Serial.println("MPU6050 initialized succesfully.");
  mpu.setAccelerometerRange(MPU6050_RANGE_8_G);  // sets the accelerometer's measurement range to ±8g
  mpu.setGyroRange(MPU6050_RANGE_250_DEG); // sets the gyroscope's measurement range to ±500 degrees/second.
  mpu.setFilterBandwidth(MPU6050_BAND_94_HZ); // configures the DLPF bandwidth to 94 Hz, to reduce high-frequency noise.
  delay(250); // brief pause for stabilization
 
  // MPU6050 calibration
  float sum = 0.0;
  for (int i = 0; i < samples; i++) {
    sensors_event_t a, g, temp;
    mpu.getEvent(&a, &g, &temp);
    sum += g.gyro.z;
    delay(5);
  }
  gyroZ_offset = sum / samples; // gets the average yaw offset in the static robot
  Serial.print("MPU Calibration completed.  Calculated offset: ");
  Serial.println(gyroZ_offset);
  Serial.println("Orientation control fully initialized...");
}
 
// Setup for Color Detection with TCS color sensors
void initColorSensors() {
  Serial.println("Iniciando sensores de color.");
  floorTcs.begin(); // start i2c tcs color sensor
  Serial.println("Color sensors initialized...");
}
 
// Setup for Ultrasonic Sensors
void initUltrasonic() {
  // No setup needed; sonars declared in the header
  Serial.println("Ultrasonic sensor initialized...");
}
 
 // Setup for OpenMV
void initVision() {
  Serial1.begin(115200);
  delay(100);
  Serial.println("Artificial vision initialized...");
}
// Setup for State Logic Functionalities
void initStateLogic() {
  setTargetYaw(0.0);
  Serial.println("State logic initialized...");
}
 
void initHeadlights(int ledBrightness) {
  analogWrite(LED_HEADLIGHT_PWM, ledBrightness);
  delay(100);
  Serial.print("Headlights initialized...");
}

// Start button function.
// Blocks the program until the button is pressed.
void waitForStartButton() {
  pinMode(buttonPin, INPUT);  // configures the button and led pin
  pinMode(ledPin, OUTPUT);
  Serial.println("Ready for initiation. Waiting for button press...");
  digitalWrite(ledPin, HIGH); // turns on the LED indicator
 
  while (!digitalRead(buttonPin)) { // while the button is not pressed
    delay(5);
  }
 
  delay(1000);
  digitalWrite(ledPin, LOW);  // turns off the LED indicator
}
 
// Movement Functions
 
// Drive forwards at a specific speed
void driveForward(int speed) {
  analogWrite(MOTOR_INA_PWM, speed);  // sets the Motor INA to the speed PWM signal
  digitalWrite(MOTOR_INB_PWM, LOW); // sets the Motor INB to LOW (0 PWM)
}
 
// Drive backwards at a specific speed
void driveBackward(int speed) {
  analogWrite(MOTOR_INA_PWM, LOW);
  digitalWrite(MOTOR_INB_PWM, speed);
}
 
// Stops motors forcefully
void stopBrake() {
  digitalWrite(MOTOR_INA_PWM, HIGH); // sets both input pins to HIGH, to create a short-circuit braking effect
  digitalWrite(MOTOR_INB_PWM, HIGH);
}
 
// Function for controlling angular position of front steering wheels with attached servomotor
void setSteeringAngle(int angle) {
  angle = constrain(angle, SERVO_LEFT, SERVO_RIGHT);  // constrains the angle to limit the maximum and minimum servo angles
  steeringServo.write(angle); // writes the given angle to the servo motor

  /*Serial.print("Servo angle set to: "); // debugging
  Serial.print(angle);
  Serial.println("°"); // prints the servo angle to the serial monitor*/
}
 
// Encoder Interrupt Service Routine to count pulses
void encoderISR() {
  encoderPulseCount++;
}

// Function to move a specific distance (cm) while keeping orientation
void encoderDelayOrientation(unsigned long cm) {
  encoderPulseCount = 0; // Reset encoder pulse count
  int pulsesRequired = PULSES_PER_CM * 5 * cm; // Calculate required pulses
  Serial.print("PULSES REQUIRED ORIENTATION: ");
  Serial.println(pulsesRequired);

  unsigned long lastUpdateTimeEO = 0UL; // Track last orientation update

  while (1) {
    unsigned long nowEO = micros();

    // Update orientation only every 25 ms
    if (nowEO - lastUpdateTimeEO >= 25000UL) {
      updateOrientation();
      lastUpdateTimeEO = nowEO;
    }

    keepOrientation();   // Maintain orientation
    delay(3);            // Small delay to prevent CPU overload

    Serial.print("Missing pulses: ");
    Serial.println((pulsesRequired - encoderPulseCount + 2));

    // Exit loop when required pulses are reached
    if (((pulsesRequired - encoderPulseCount) <= 0)) {
      break;
    }
  }
  Serial.println("Finished Encoder Delay Orientation");
}

// Function to move a specific distance (cm) without orientation correction
void encoderDelay(unsigned long cm) {
  encoderPulseCount = 0; // Reset encoder pulse count
  int pulsesRequired = PULSES_PER_CM * 5 * cm; // Calculate required pulses
  Serial.print("PULSES REQUIRED: ");
  Serial.println(pulsesRequired);

  unsigned long lastUpdateTimeE = 0UL; // Track last orientation update

  while (1) {
    unsigned long nowE = micros();

    // Update orientation only every 25 ms
    if (nowE - lastUpdateTimeE >= 25000UL) {
      updateOrientation();
      lastUpdateTimeE = nowE;
    }

    delay(3); // Small delay to prevent CPU overload

    Serial.print("Missing pulses: ");
    Serial.println((pulsesRequired - encoderPulseCount + 2));

    // Exit loop when required pulses are reached
    if (((pulsesRequired - encoderPulseCount) <= 0)) {
      break;
    }
  }
  Serial.println("Finished Encoder Delay");
}

// Function for movement with obstacle detection and evasion
bool safeDelayEvasionEncoder(unsigned long cm) {
  encoderPulseCount = 0;  // Reset encoder pulse count
  int pulsesRequired = PULSES_PER_CM * 5 * cm; // Calculate required pulses
  Serial.print("PULSES REQUIRED: ");
  Serial.println(pulsesRequired);

  bool obstacleFound = false;
  unsigned long lastUpdateTimeEE = 0UL; // Track last orientation update

  while (1) {
    unsigned long nowEE = micros();

    // Update orientation only every 25 ms
    if (nowEE - lastUpdateTimeEE >= 25000UL) {
      updateOrientation();
      lastUpdateTimeEE = nowEE;
    }

    keepOrientation(); // Maintain orientation
    delay(5);

    // If obstacle detected, handle evasion
    if (obstacleDetected()) {
      Serial.print("An obstacle was detected during evasionDelay");
      handleEvasion();
      obstacleFound = true;
      Serial.println("obstacleFound = TRUE");
    }

    Serial.print("Remaining steps: ");
    Serial.print((pulsesRequired - encoderPulseCount + 2));
    Serial.println(" pulses");

    delay(5);

    // Exit loop when required pulses are reached
    if (((pulsesRequired - encoderPulseCount) <= 0)) {
      break;
    }
  }

  Serial.println("Finished Delay Encoder");
  return obstacleFound;
}
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

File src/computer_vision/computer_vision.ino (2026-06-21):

#include <SPI.h>
#include <Pixy2.h>
#include <Servo.h>

#define SERVO_PIN 6
#define SERVO_STRAIGHT 85
#define SERVO_LEFT 50
#define SERVO_RIGHT 110

Pixy2 pixy; // Objeto Pixy
Servo steeringServo; // Objeto Servo

void setup() {
  Serial.begin(115200); // Initializes Serial Bus at 115200 bauds for Pixycam
  Serial.print("Initializing PixyCam...");

  pixy.init(); 
  Serial.println(" PixyCam initialized.");

  steeringServo.attach(SERVO_PIN);
  setSteeringAngle(SERVO_STRAIGHT);
}

void loop() {
  int i = pixy.ccc.getBlocks();

  if (i > 0) {
    for (int j = 0; j < i; j++) {
      if (pixy.ccc.blocks[j].m_signature == 2) { 
        Serial.println("RED detected. Turning RIGHT.");
        setSteeringAngle(SERVO_RIGHT);
        delay(100);
        break; 
      } else if (pixy.ccc.blocks[j].m_signature == 1) {
        Serial.println("GREEN detected. Turning LEFT.");
        setSteeringAngle(SERVO_LEFT);
        delay(100);
        break; 
      }
    }
  } else {
    Serial.println("No blocks detected...");
    setSteeringAngle(SERVO_STRAIGHT);
  }

  delay(50);
}

void setSteeringAngle(int angle) {
  angle = constrain(angle, SERVO_LEFT, SERVO_RIGHT);
  steeringServo.write(angle);
}

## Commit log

2025-07-08 Replaced the motor driver image
2025-07-08 Update 04_sensors_and_pin_configuration.md
    Edited the ultrasonic configuration.
2025-07-08 Update 06_pid_gyroscope_control.md
    Modifications and clarifications on the calibration code.
2025-07-08 Update 11_other_resources.md
    Added the ultrasonic data graph. More to add into the miscelaneous section.
2025-07-10 Uploaded the ultrasonic median filter code
2025-07-15 Uploaded the 4.2V battery img
2025-09-30 Updating Github
    [MPU Calibration Data Analysis.xlsx, Ultrasonic Sensors Data Analysis.xlsx]
2025-09-30 Added the kicad scheme
2025-11-18 Updating src/kicad_pcb directory
    [ViZio_PCB_Shield.kicad_pcb, ViZio_PCB_Shield.kicad_sch]
2025-11-18 Create kicad_pcb
2025-11-18 Document I2C bus fix and update images
2025-11-18 Update I2C bus images in hardware components documentation
2025-11-19 Update 3D model links in documentation
    Added final and international 3D model links for the chassis.
2025-11-19 Add link to International 3D Model for chassis
    Added link to the International 3D Model of the chassis.
2025-11-19 Update README with new chassis information
2025-11-19 Fix formatting in README.md for chassis section
2025-11-19 Fix file name for International Chassis in README
    Corrected the file name for the International Chassis in the table.
2025-11-19 Update README with new chassis model information
2025-11-19 Updated avoidWallPID function details
    Updated the section on the avoidWallPID function to clarify its purpose, operation, and the conditions under which it runs. Added detailed explanations for timing control, error calculation, and yaw adjustment logic.
2025-11-19 Refine documentation for ultrasonic distance sensing
    Updated explanations for sonar sensor setup and PD control logic.
2025-11-19 Fix formatting and update ultrasonic distance sensing doc
2025-11-19 Enhance documentation for avoidWallPID function
    Expanded the explanation of the avoidWallPID function, detailing its purpose, operation, timing control, setup, lateral PD control, yaw adjustment logic, and new target yaw application.
2025-11-19 Replace safeDelay with safeDelayColor in evasion logic
    Updated delay functions to use safeDelayColor for better handling of yaw error during evasion.
2025-11-19 Document performance improvement by soldering MPU
    Added a note on the performance improvement achieved by soldering the MPU to reduce vibrations.
2025-11-19 Update Pixy calibration instructions for clarity
    Clarified instructions for Pixy calibration regarding lens covering during initialization.
2025-11-21 Update 01_project_overview.md
    Updated the Flow Diagram
2026-06-21 ViZio IV update
    [AxleAndSupport.stl, Lig1.stl, Lig2.stl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]
2026-06-21 Refine AWB and auto-gain description in documentation
    Clarified the explanation of AWB and auto-gain settings for camera initialization.
2026-06-21 Refine AWB and auto-gain description in documentation
    Clarified the explanation of AWB and auto-gain settings for camera initialization, correcting terminology and improving readability.
2026-06-21 Increase steering angle from 50° to 55°
2026-06-21 Update ViZio IV chassis embed link
2026-06-21 Fix link for 2026 Chassis Models in README
    Updated link for 2026 Chassis Models to point to documentation.
2026-06-21 Update README with new video sections
    Added a new section for the differential assembly video
2026-06-22 Replace differential assembly video thumbnail link
    Updated video links in README for differential assembly.
2026-06-22 Update hardware components documentation
    Removed outdated components PixyCam 2.1 and TCS3200 Color Sensor from the hardware documentation. Added a new section for removed components.
2026-06-22 Update current draw information for OpenMV H7
2026-06-22 Revise hardware components section and update PCB details
    Removed sections on original and Arduino MKR1010 circuit designs, and added details about the new custom KiCad PCB circuit for the Mega 2560 Pro, including improvements and fixes.
2026-06-22 Fix spelling errors in computer vision documentation
    Corrected spelling errors in the explanation of camera settings and white balance configuration.
2026-06-22 Fix spelling errors in computer vision documentation
    Corrected spelling errors in the Size Filtering and Data Transmission section.
2026-06-22 Corrected sensor model from TCS34725 to TCS3472
2026-06-23 Remove sensor placement logic section
    Removed section on sensor placement logic, including ultrasonic sensors, PCB circuit, and camera pitch angle adjustments.
2026-06-23 Remove component selection section from documentation
    Removed the component selection section detailing the controller, artificial vision, distance sensing, and color detection components. Simplified the explanation of sensor choices and alternatives.
